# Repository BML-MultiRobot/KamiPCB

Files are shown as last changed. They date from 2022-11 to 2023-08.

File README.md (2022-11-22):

# KamiPCB
Custom PCB for the Kamigami Robot

Base PCB

PCB with Motor Driver and IMU

PCB with RaspberryPi plugged in

## Features:

- GPIO pinout for a 40 pin RaspberryPi Zero 2W

- Footprint for a [slide switch](https://www.digikey.com/en/products/detail/w%C3%BCrth-elektronik/450405020524/11631973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).
    - On position: RaspberryPi Powers On
    - Off position: Charging port is active(can connect the charger)

- Two footprints for [JST connectors](https://www.adafruit.com/product/1769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)
    - Bottom one for [LiPo battery](https://www.adafruit.com/product/2011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) connection
    - Top one for [LiPo Batter Charger](https://www.adafruit.com/product/259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)

- Pinout for the [motor driver](https://www.sparkfun.com/products/14451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)
    - simply just stacked on via header pins
    - motor leads are routed to the side for easy installation

- Pinout for [8 channel ADC](https://www.adafruit.com/product/856)
    - one channel is already connected to the battery leads for battery voltage measurements

- Footprints for voltage divider step down (all 0805 SMD footprints)
    - one 100kOhm resistor
    - one 180kOhm resistor
    - one 0.1uF capacitor

- Pinout for [9 axis IMU](https://www.adafruit.com/product/3463)

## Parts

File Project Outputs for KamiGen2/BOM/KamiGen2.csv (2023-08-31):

Comment | Description | Designator | Footprint | LibRef | Quantity
C1206C104K3RACTU | CAP CER 0.1UF 25V 10% X7R 1206 | C1, C2, C5, C6, C7, C8, C9, C10, C11, C12 | FP-C1206C-EB-MFG | CMP-00100-1 | 10
T491A106K010AT | Capacitor, Tantalum, 10 uF, +/- 10%, 10 V, -55 to 125 degC, 2-Pin SMD (1206), RoHS, Tape and Reel | C3, C4 | KEMT-A-3216-18-2_M | CMP-2000-05172-1 | 2
BZY55B3V3_RBG | Diode | D1, D2, D3 | BZY55B3V3RBG | BZY55B3V3_RBG | 3
150120GS75000 | LED GREEN CLEAR 1206 SMD | D4 | FP-150120GS75000-MFG | CMP-1426-00014-2 | 1
150120BS75000 | SMD mono-color Chip LED, WL-SMCW, Blue | D5 | 1206_A | CMP-1426-00015-1 | 1
503763-0491 | Connector | J1 | 5037630491 | 503763-0491 | 1
S2B-PH-SM4-TB(LF)(SN) | Connector Header Surface Mount, Right Angle 2 position 0.079 (2.00mm) | J2, J4 | JST_S2B-PH-SM4-TB(LF)(SN) | CMP-064-000001-2 | 2
40 Pin Header (2.54mm) | WR-PHD Straight Male, PCB Header, Through Hole, 2 Rows, 40 Contacts, 2.54mm Pitch | J3 | 61304021121 | CMP-00112-1 | 1
WSL0805R0500FEA |  | R1, R2 | RESC2013X46X38ML25T25 | CMP-2001-04327-1 | 2
CRCW080510K0FKEA | RES Thick Film, 10kO, 1%, 0.125W, 100ppm/°C, 0805 | R3, R5, R6 | FP-CRCW0805-e3-IPC_A | CMP-2001-04908-2 | 3
ERJ-6ENF1502V | RES SMD 15K OHM 1% 1/8W 0805 | R4 | FP-ERJ6EN-IPC_C | CMP-2001-04439-3 | 1
ERJ-14NF1001U | Res Thick Film 1210 1K Ohm 1% 1/2W ±100ppm/°C Molded SMD Embossed Carrier T/R | R7 | RESC3225X70X50LL20T20 | CMP-00078-1 | 1
CRGH0805F787R | Resistor | R8, R9 | RESC2013X65N | CRGH0805F787R | 2
ERJ-6RBD2000V | Resistor | R10, R11 | RESC2012X70N | ERJ-6RBD2000V | 2
JS102000SAQN | Slide Switch, Js Series, SPDT, Right Angle, SMD, 1 ma Rohs Compliant: Yes | SW1 | FP-JS102000SAQN-MFG | CMP-00098-1 | 1
TB6612FNG | Driver IC for Dual DC Motor, 15 V, -20 to 85 degC, 24-Pin SSOP, RoHS, Tape and Reel | U1, U2 | TOSH-SSOP-24_M | CMP-1773-00001-1 | 2
AD8544ARZ | Operational Amplifier, Quad, 1 Mhz, 4, 0.92 V/ S, 2.7V To 5.5V, Soic, 14 Rohs Compliant: Yes | U3 | ADI-R-14_M | CMP-00114-1 | 1
MCP3004-I/SL | 4-Channel Single ADC SAR 200ksps 10-bit Serial Automotive 14-Pin SOIC N Tube | U4 | SOIC-SL14_L | CMP-014-000002-1 | 1

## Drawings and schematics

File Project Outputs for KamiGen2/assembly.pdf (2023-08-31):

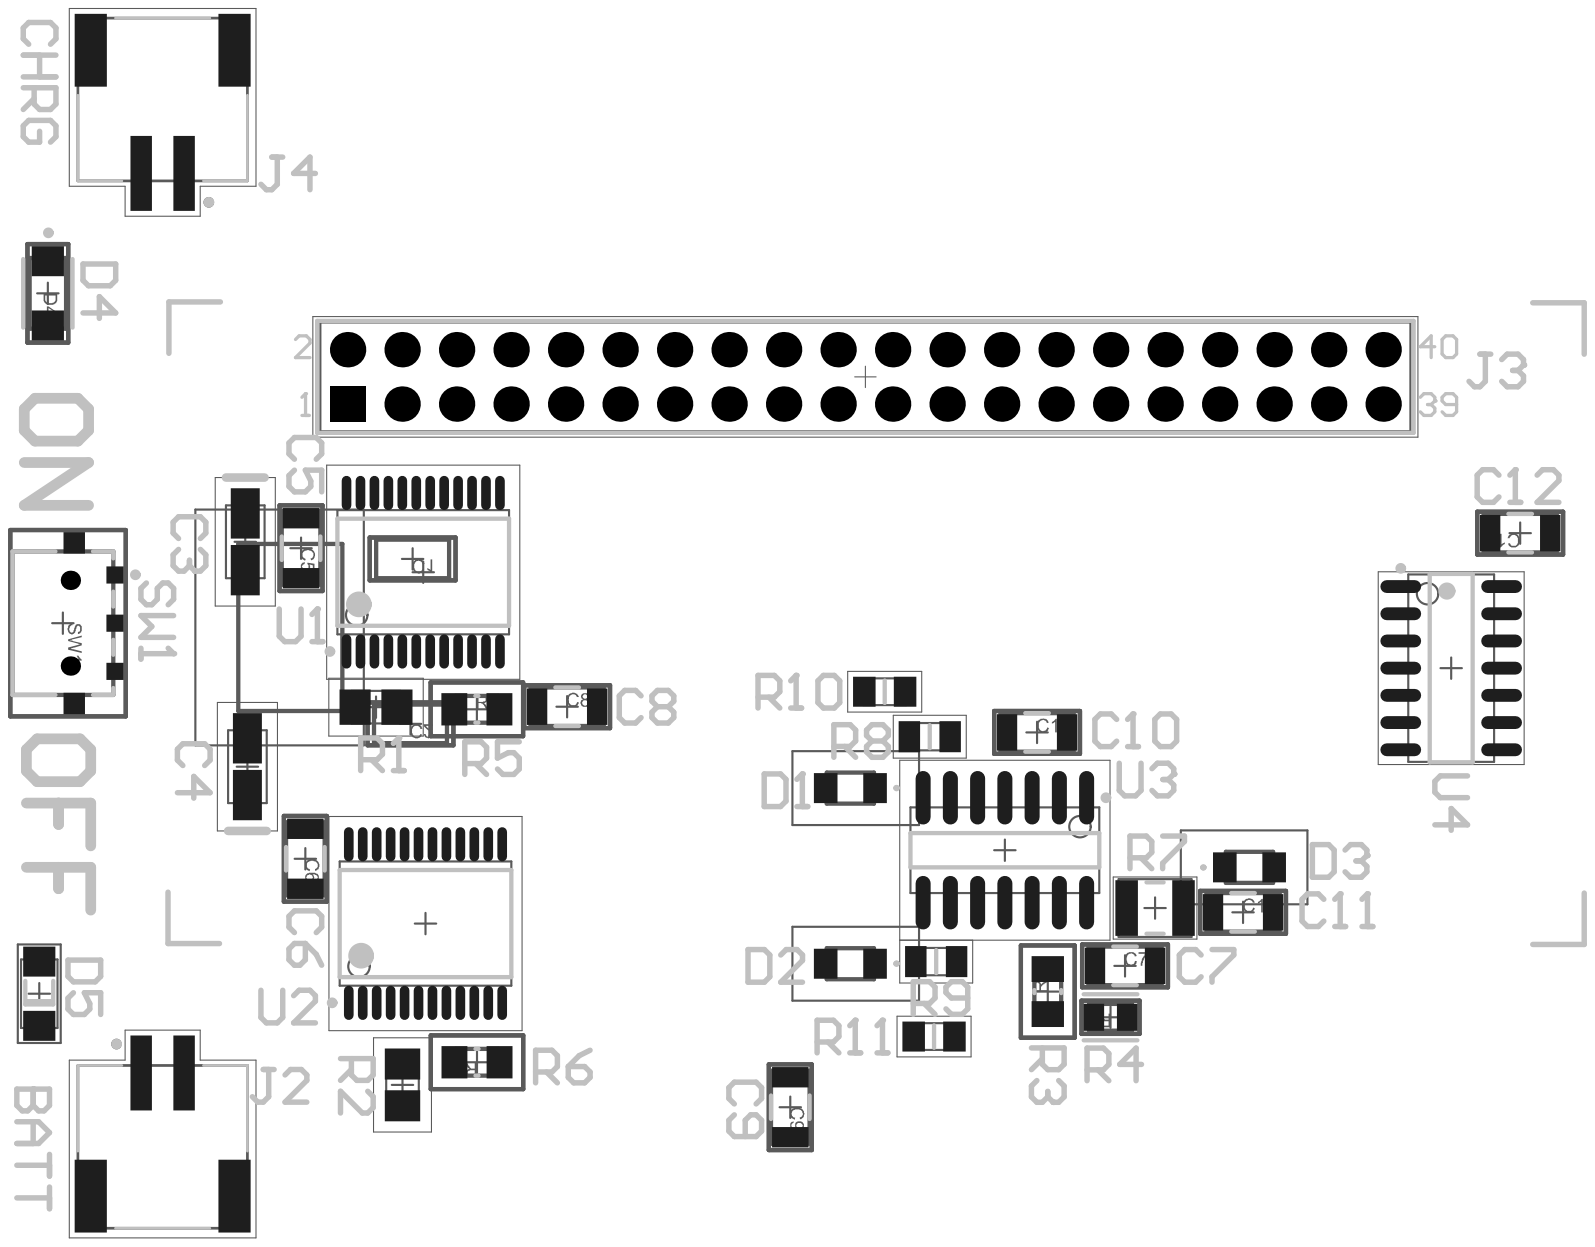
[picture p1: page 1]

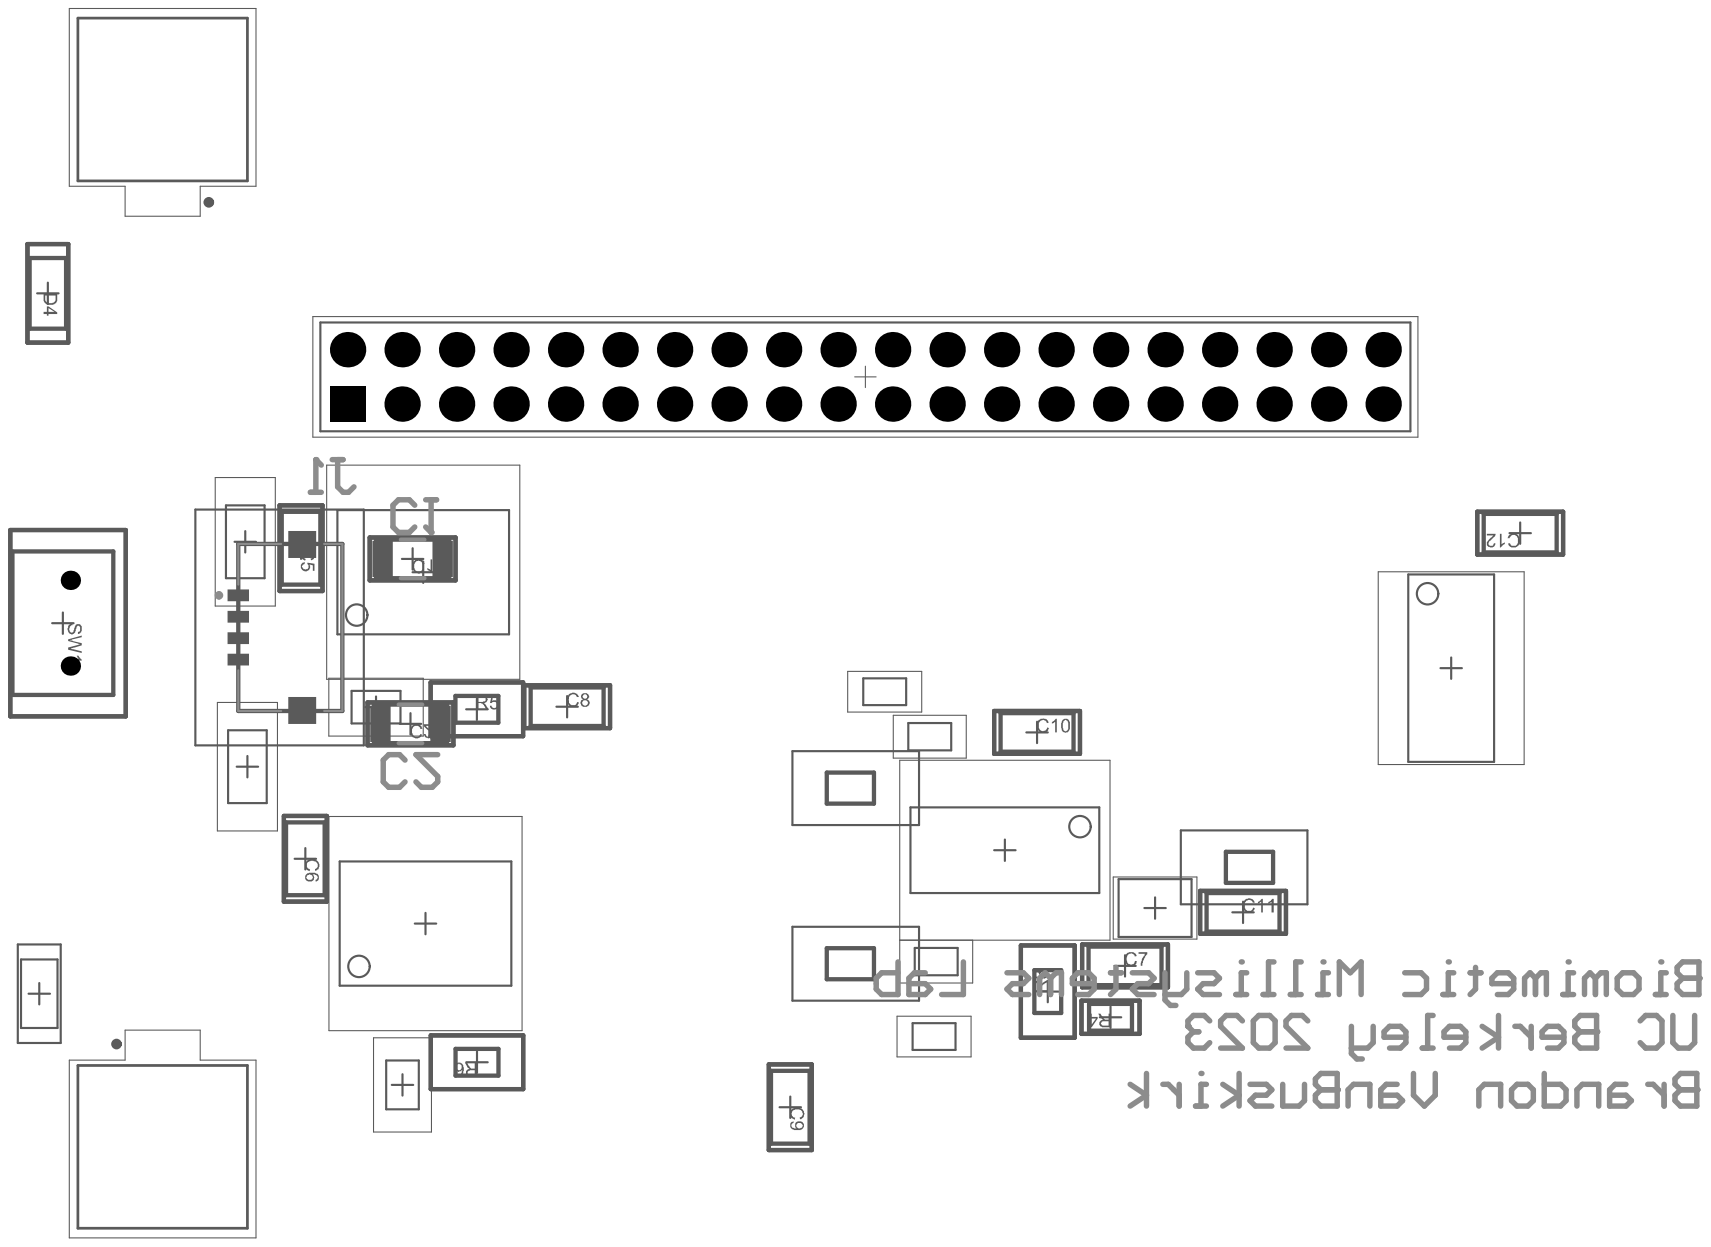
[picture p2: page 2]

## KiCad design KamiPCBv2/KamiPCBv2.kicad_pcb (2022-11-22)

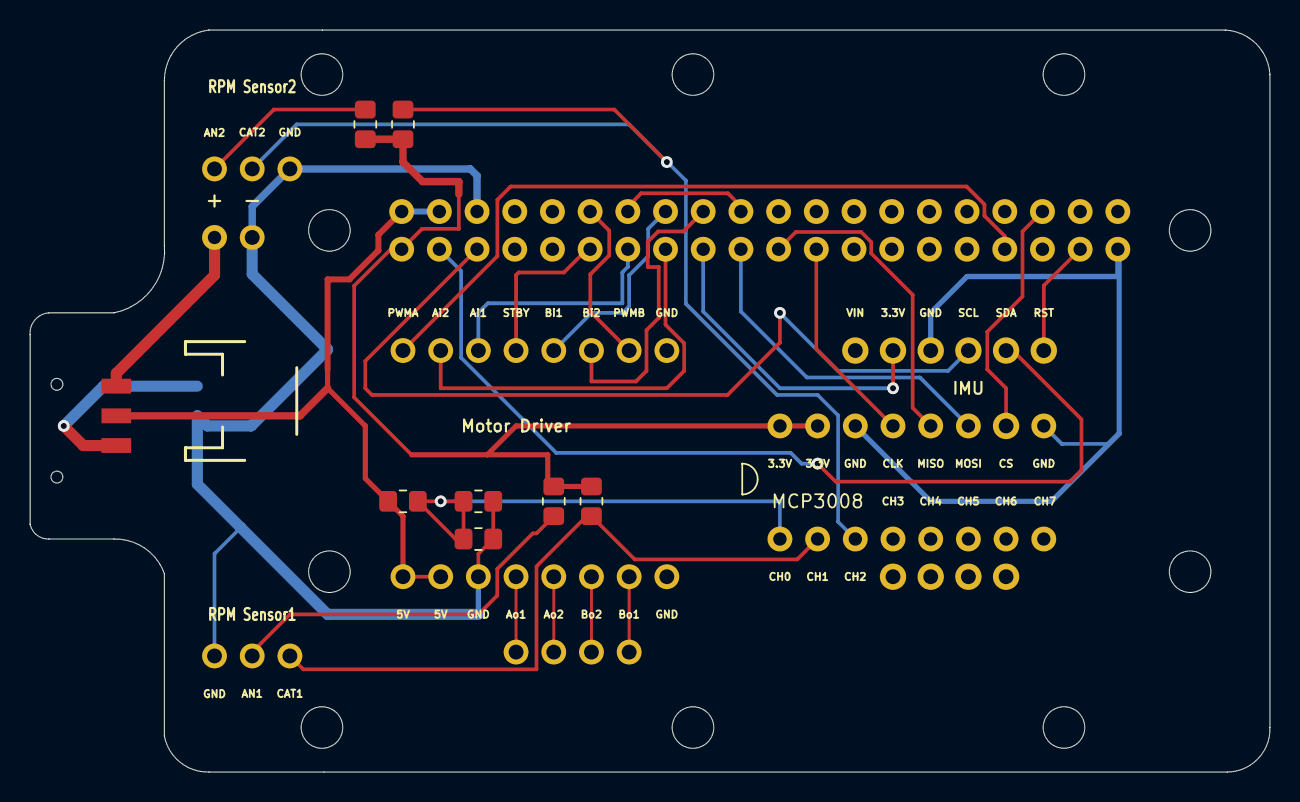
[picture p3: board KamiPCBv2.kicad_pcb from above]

Board: 2 copper layers, 83.6 x 50.0 mm, 4 parts (0 on the bottom side), 5 nets.

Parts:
FID1: FIDUCIAL""; FIDUCIAL_1MM
JP1: 1X06_ROUND_70
RPI1: KamiPCB; PI_BONNET_NODIM
X1: JSTPH2

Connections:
3.3V: JP1.5, RPI1.1, RPI1.17
5.0V: RPI1.2, RPI1.4
GND: JP1.4, RPI1.6, RPI1.9, RPI1.14, RPI1.20, RPI1.25, RPI1.30, RPI1.34, RPI1.39
SCL: JP1.3, RPI1.5
SDA: JP1.2, RPI1.3

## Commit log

2022-11-22 first five iterations
    [KamiPCB-B_Cu.gbr, KamiPCB-B_Mask.gbr, KamiPCB-B_Paste.gbr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]
2023-08-31 Add files via upload
    Files of Second Generation Kamigami PCB(note: PRE-engineer review).
    [KamiGen2.PcbDoc, KamiGen2.PrjPcb, KamiGen2.SchDoc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]
